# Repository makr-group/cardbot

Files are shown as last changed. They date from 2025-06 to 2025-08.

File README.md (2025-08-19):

    ╔══════════════════════════════════════════════════════════════════╗
    ║                                                                  ║
    ║     ██████╗ █████╗ ██████╗ ██████╗ ██████╗  ██████╗ ████████╗    ║
    ║    ██╔════╝██╔══██╗██╔══██╗██╔══██╗██╔══██╗██╔═══██╗╚══██╔══╝    ║
    ║    ██║     ███████║██████╔╝██║  ██║██████╔╝██║   ██║   ██║       ║
    ║    ██║     ██╔══██║██╔══██╗██║  ██║██╔══██╗██║   ██║   ██║       ║
    ║    ╚██████╗██║  ██║██║  ██║██████╔╝██████╔╝╚██████╔╝   ██║       ║
    ║     ╚═════╝╚═╝  ╚═╝╚═╝  ╚═╝╚═════╝ ╚═════╝  ╚═════╝    ╚═╝       ║
    ║                                                                  ║
    ╚══════════════════════════════════════════════════════════════════╝
    
      █▄▄ █▄█   █▀▄▀█ ▄▀█ █▄▀ █▀█
      █▄█ ░█░   █░▀░█ █▀█ █░█ █▀▄

**Cardbot** is a open source robotics project desinged to bring low costs entry level robots
to students and kids. This project was started by the non-profit Makr Group (aka Makr) to
bring robotics to under served communities in Omaha, Nebraska, USA. With the goal to
kickstart intrest in technology and robotics. The Project is ongoing and slowly growing with 
the capbilites of the robots.

Cardbot is shared under the **Creative Commons Attribution-ShareAlike 4.0 International** license.

## Current Features

- Controller driven Bots with a programmable autonomus mode
- Phone Driven Bots (Broken)
- 3D printer files
- Laser cutter files
- Build Instuctions

## Planned Features

- Full programming instuctions
- Class lesson plans
- Alternative Build Lists

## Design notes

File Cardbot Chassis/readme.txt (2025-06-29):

This folder contains all files related to the cardbot chassis.

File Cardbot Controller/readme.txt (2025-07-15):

Code and Files for Cardbot controllers.

Adruino IDE addons:

Board:
arduino-esp32 by expressif: https://github.com/espressif/arduino-esp32

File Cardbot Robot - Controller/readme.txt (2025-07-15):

Code for controller based Cardbots.

Adruino IDE addons:

Board:
arduino-esp32 by expressif: https://github.com/espressif/arduino-esp32

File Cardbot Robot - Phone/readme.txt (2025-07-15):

Code for phone/wifi controlled cardbots.

Adruino IDE addons:

Board:
arduino-esp32 by expressif: https://github.com/espressif/arduino-esp32

External Libaries:
AsyncTCP by ESP32Async: https://github.com/ESP32Async/AsyncTCP
ESPAsyncWebServer by ESP32Async: https://github.com/ESP32Async/ESPAsyncWebServer
ArduinoJson by Benoît Blanchon: https://github.com/bblanchon/ArduinoJson

Plugins:
arduino-littlefs-upload by Earle F. Philhower, III: https://github.com/earlephilhower/arduino-littlefs-upload

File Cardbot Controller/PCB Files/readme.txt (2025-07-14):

Files for Controller PCB both Gerber and KiCad.

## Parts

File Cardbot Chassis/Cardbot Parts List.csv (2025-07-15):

Item | Link | Per Kit
Jumpers | https://www.amazon.com/dp/B07XMH7MPL?ref_=ppx_hzsearch_conn_dt_b_fed_asin_title_3&th=1 | -
Red | - | 3
Black | - | 2
White | - | 2
Orange | - | 2
Yellow | - | 1
Purple | - | 1
Grey | - | 2
Brown | - | 2
Green | - | 1
Blue | - | 2
Active Components
Xaio Esp32C3 | https://www.digikey.com/en/products/detail/seeed-technology-co-ltd/113991054/16652880 | 1
5v Buck Converters | https://www.amazon.com/dp/B0BVFTSSSC?ref=ppx_yo2ov_dt_b_fed_asin_title&th=1 | 1
H Bridge | https://www.digikey.com/en/products/detail/adafruit-industries-llc/4489/11594498 | 2
TT Motor | https://www.amazon.com/dp/B09N6NXP4H?ref=ppx_yo2ov_dt_b_fed_asin_title | 2
9v Battery | https://www.amazon.com/dp/B07MWPHV25?ref=ppx_yo2ov_dt_b_fed_asin_title | 1
Passive Componets
Bread Board | https://www.amazon.com/dp/B07LFD4LT6?ref=ppx_yo2ov_dt_b_fed_asin_title | 1
Button (Short) | https://www.amazon.com/dp/B01CGMP9GY?ref=ppx_yo2ov_dt_b_fed_asin_title | 1
7 pin Headers | https://www.digikey.com/en/products/detail/adam-tech/PH1-07-UA/9830505 | 2
Switch | https://www.amazon.com/dp/B099MRCDG8?ref=ppx_yo2ov_dt_b_fed_asin_title&th=1 | 1
9v Battery Lead | https://www.amazon.com/dp/B083QFMXXW?ref=ppx_yo2ov_dt_b_fed_asin_title | 1
2-pos Terminal Block | https://www.amazon.com/dp/B01MT4LC0F?ref=ppx_yo2ov_dt_b_fed_asin_title | 1
Chassis Componets
Body | https://github.com/makr-group/cardbot/tree/main/cardbot%20chassis | 1
Connor Bracket | https://github.com/makr-group/cardbot/tree/main/cardbot%20chassis | 2
Connor Connector | https://github.com/makr-group/cardbot/tree/main/cardbot%20chassis | 4
Tail | https://github.com/makr-group/cardbot/tree/main/cardbot%20chassis | 1
Battery Holder | https://github.com/makr-group/cardbot/tree/main/cardbot%20chassis | 1
Pin | https://github.com/makr-group/cardbot/tree/main/cardbot%20chassis | 2

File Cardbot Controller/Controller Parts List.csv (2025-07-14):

Item | Link | Per Controller
Xaio Esp32C3 | https://www.digikey.com/en/products/detail/seeed-technology-co-ltd/113991054/16652880 | 1
Buttons (Tall) | https://www.digikey.com/en/products/detail/e-switch/TL1105BF160Q/1358 | 4
Controller PCB | https://github.com/makr-group/cardbot/tree/582c8274fbbf508515f54be0faa1b344a32cff6f/cardbot_%20controller_controlled/controller/PCB%20files | 1
Button Cap | https://github.com/makr-group/cardbot/tree/582c8274fbbf508515f54be0faa1b344a32cff6f/cardbot_%20controller_controlled/controller/3d-printed%20files | 1
Battery Holder | https://github.com/makr-group/cardbot/tree/582c8274fbbf508515f54be0faa1b344a32cff6f/cardbot_%20controller_controlled/controller/3d-printed%20files | 1
Bottom Plate | https://github.com/makr-group/cardbot/tree/582c8274fbbf508515f54be0faa1b344a32cff6f/cardbot_%20controller_controlled/controller/3d-printed%20files | 1
Face Plate | https://github.com/makr-group/cardbot/tree/582c8274fbbf508515f54be0faa1b344a32cff6f/cardbot_%20controller_controlled/controller/3d-printed%20files | 1

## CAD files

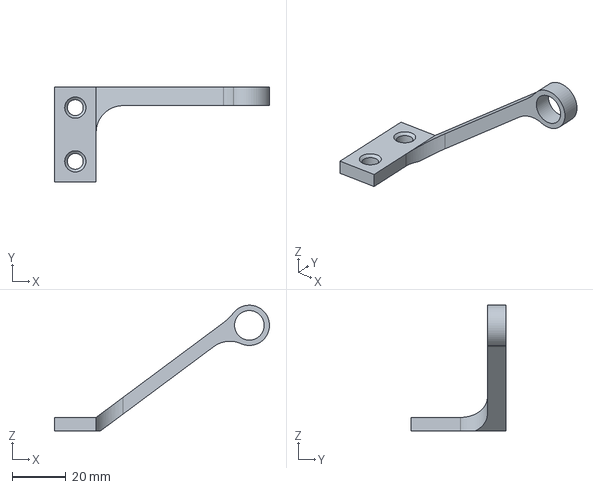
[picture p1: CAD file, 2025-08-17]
Cardbot Chassis/Cardbot Body - Tail.step
80.0 x 35.5 x 46.7 mm

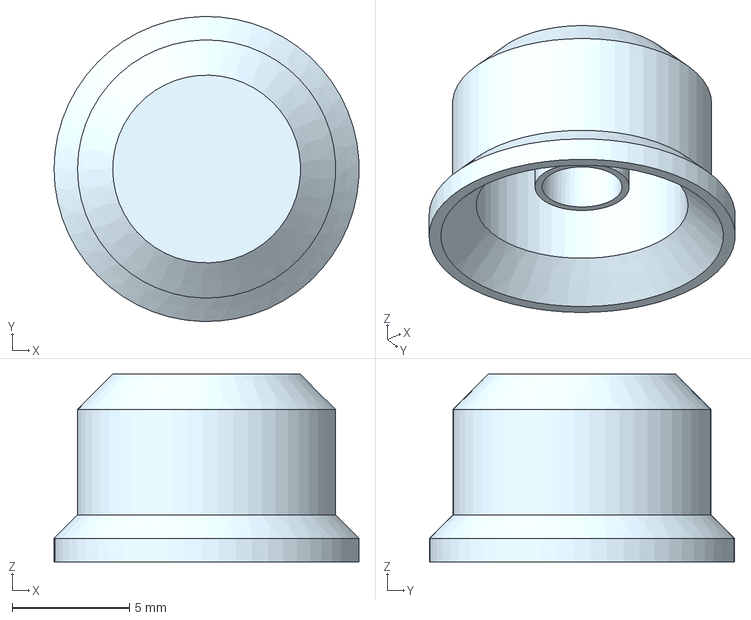
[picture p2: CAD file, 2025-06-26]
Cardbot Controller/3d-printed Files/Controller - Button Cap.step
13.0 x 13.0 x 8.00 mm

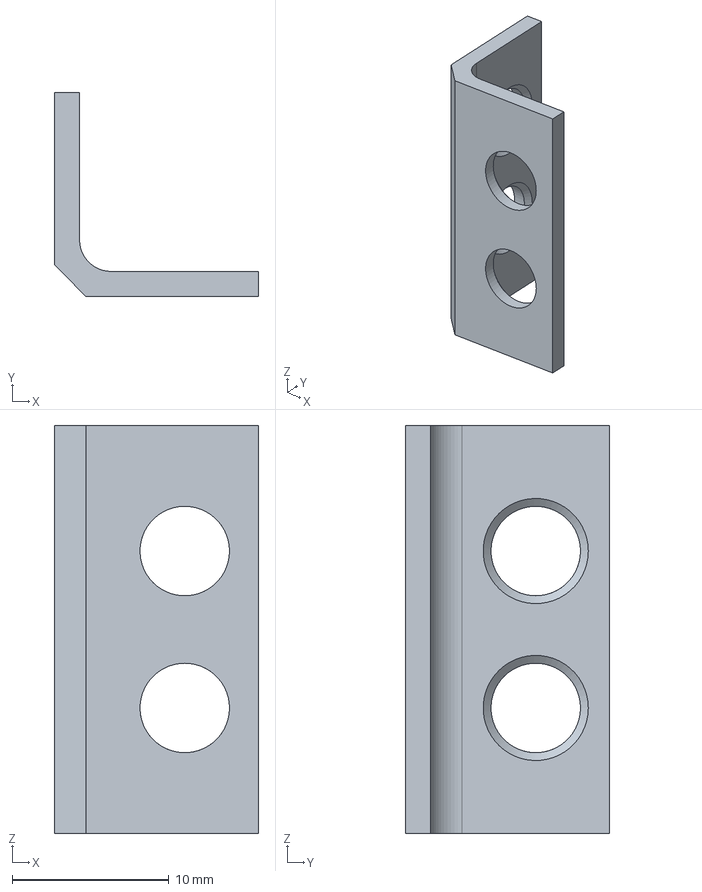
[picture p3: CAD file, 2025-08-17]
Cardbot Chassis/Cardbot Body - Corner Bracket.step
13.0 x 13.0 x 26.0 mm

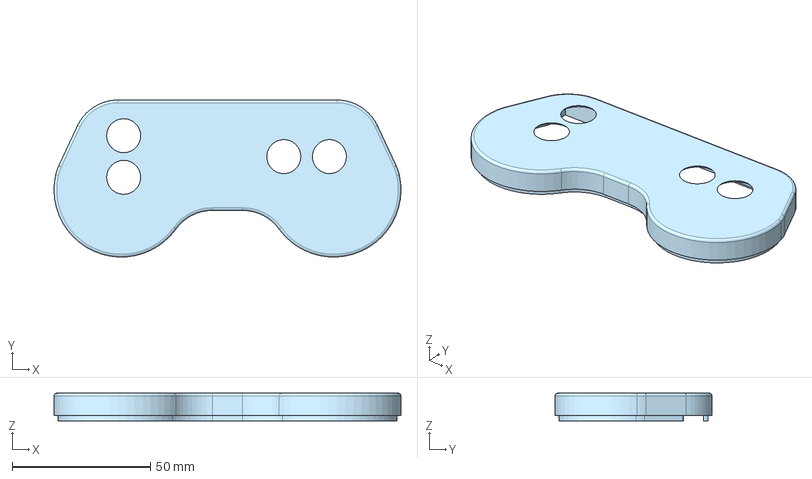
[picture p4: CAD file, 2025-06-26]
Cardbot Controller/3d-printed Files/Controller - Face Plate.step
125.7 x 56.9 x 10.0 mm

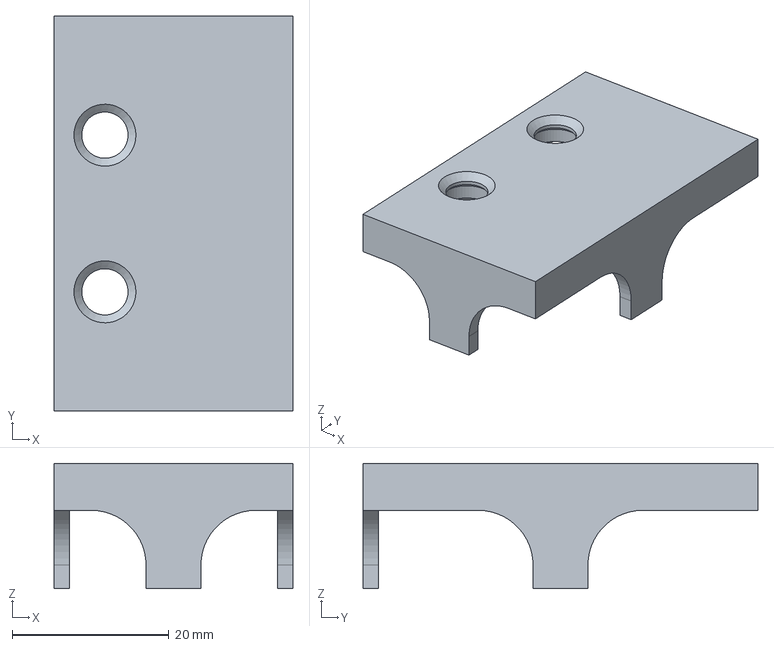
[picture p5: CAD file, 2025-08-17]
Cardbot Chassis/Cardbot Body - Battery Tray.step
30.5 x 50.4 x 16.0 mm

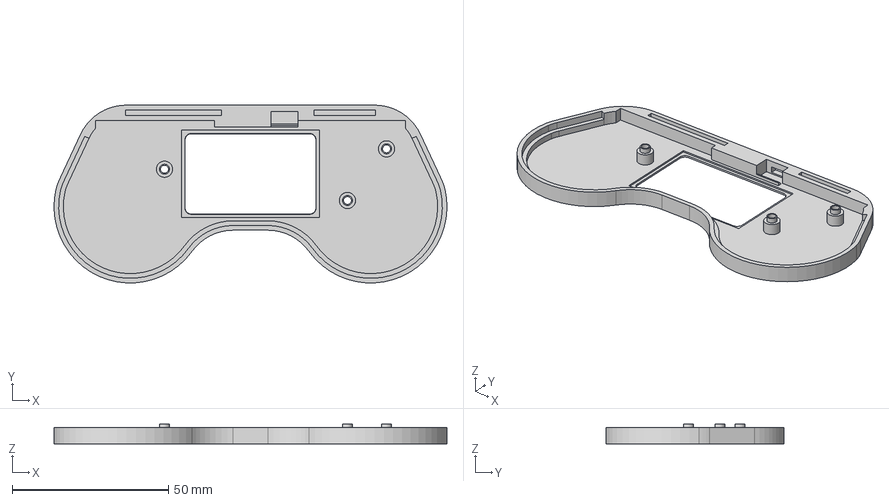
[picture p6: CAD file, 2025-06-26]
Cardbot Controller/3d-printed Files/Controller - Bottom Plate.step
125.7 x 56.9 x 6.25 mm

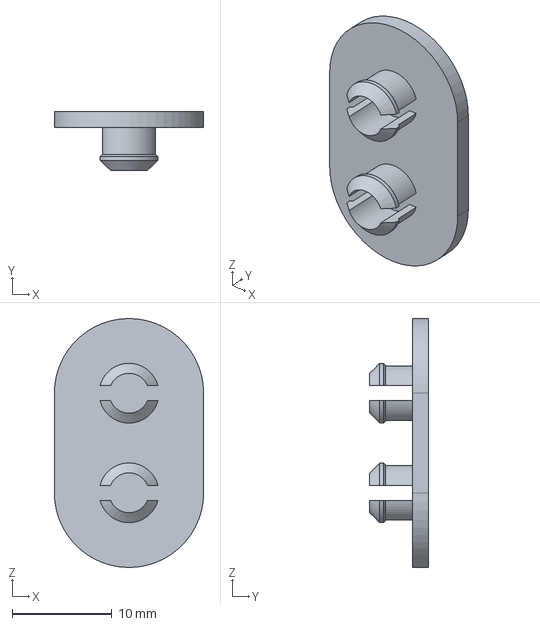
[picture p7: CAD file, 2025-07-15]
Cardbot Chassis/Cardbot Body - Corner Connector.step
15.0 x 5.90 x 25.0 mm

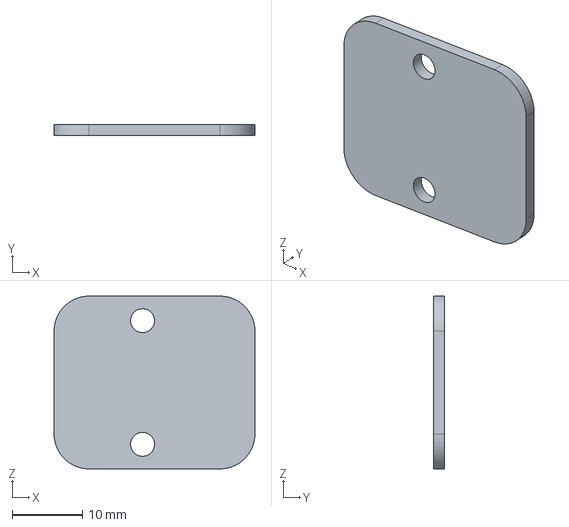
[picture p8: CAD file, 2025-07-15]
Cardbot Chassis/Cardbot Body - Motor Plate.step
28.6 x 1.60 x 24.6 mm

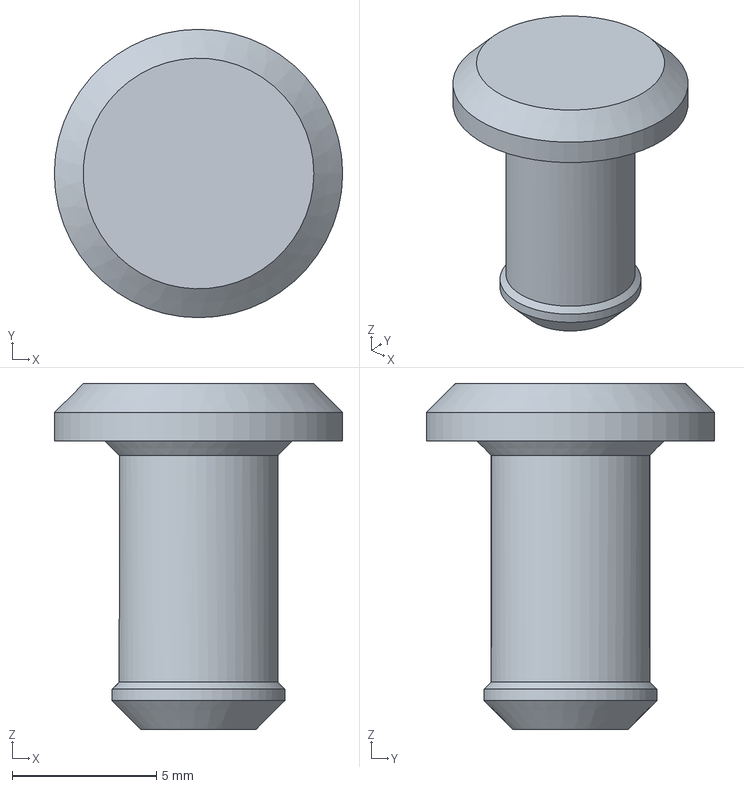
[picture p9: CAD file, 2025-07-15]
Cardbot Chassis/Cardbot Body - Tail Pin.step
10.0 x 10.0 x 12.0 mm

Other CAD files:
Cardbot Controller/3d-printed Files/Controller - Battery Holder.step
Cardbot Chassis/Cardbot Body - Battery Tray.stl
Cardbot Chassis/Cardbot Body - Corner Bracket.stl
Cardbot Chassis/Cardbot Body - Corner Connector.stl
Cardbot Chassis/Cardbot Body - Motor Plate.stl
Cardbot Chassis/Cardbot Body - Tail Pin.stl
Cardbot Chassis/Cardbot Body - Tail.stl
Cardbot Controller/3d-printed Files/Controller - Battery Holder.stl
Cardbot Controller/3d-printed Files/Controller - Bottom Plate.stl
Cardbot Controller/3d-printed Files/Controller - Button Cap.stl
Cardbot Controller/3d-printed Files/Controller - Face Plate.stl

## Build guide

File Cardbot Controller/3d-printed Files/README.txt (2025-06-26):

STL and Step files for cardbot controllers

STLs are designed to be printed with PLA and are untested 
with PETG, ABS, and ABS.

Tested with:

Printer: Ultimaker 3 Extended
Settings:
  Material: Generic PLA
  Walls: 4
  Supports: No *
  Bed Adhesion: 5mm Skirt
Notes:
* No supports is important to keep the USB-C port clean
  of unwanted material for "Controller - Face Plate". Supports 
  might be needed if your  printer cannot handle the that length 
  of bridging.

Printer Bambu labs P1S
Settings:
  Material: Bambu Labs Basic PLA
  Walls: 4
  Wall Generator: Arachne *
  Supports: No **
Notes:
  * Arachne is required for the buttons walls classic generation
    will not print inner button caps
  
**  No supports is important to keep the USB-C port clean
    of unwanted material for "Controller - Face Plate". Supports 
    might be needed if your  printer cannot handle the that length 
    of bridging.

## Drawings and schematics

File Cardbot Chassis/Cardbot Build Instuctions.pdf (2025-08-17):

1.

+

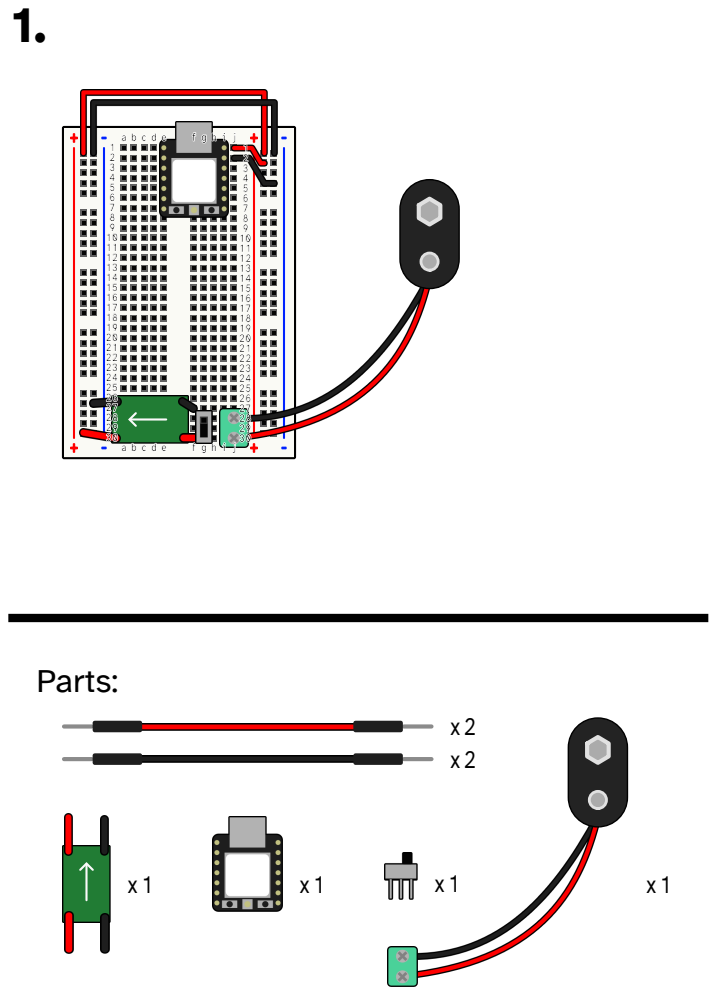
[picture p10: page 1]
Parts:

2.

+

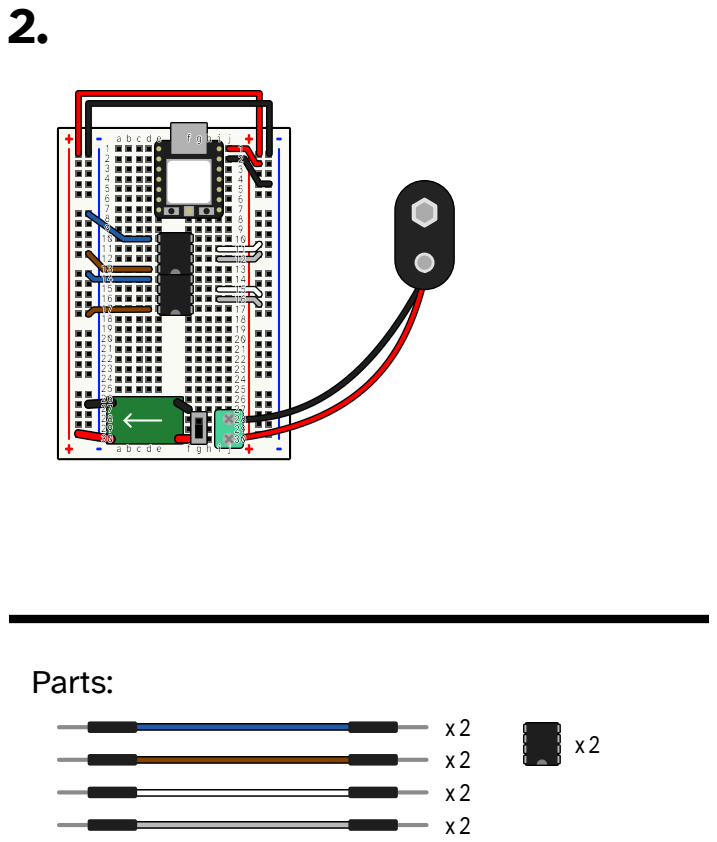
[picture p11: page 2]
Parts:

3.

# Parts: ⁺ - + -

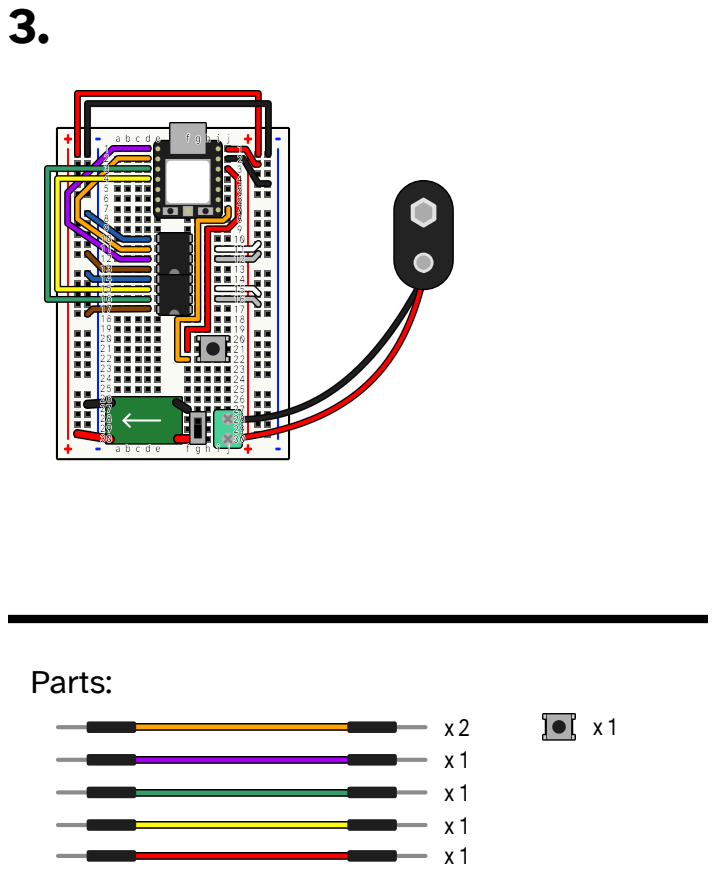
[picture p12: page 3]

4.

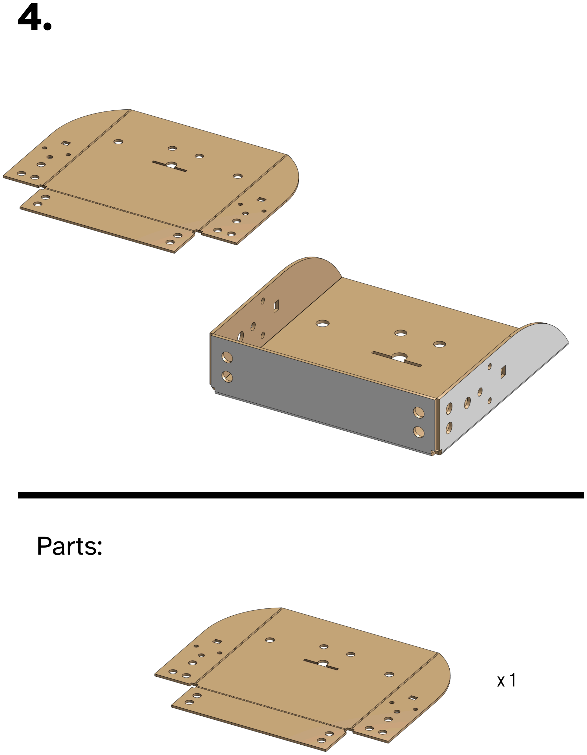
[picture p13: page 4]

# Parts:

x1

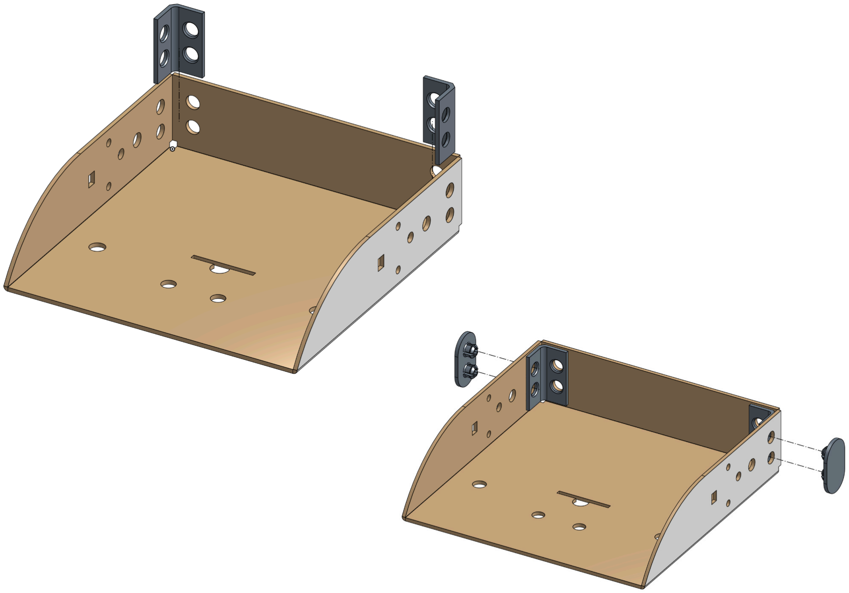
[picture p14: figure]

# Parts:

5.

x2 | x2

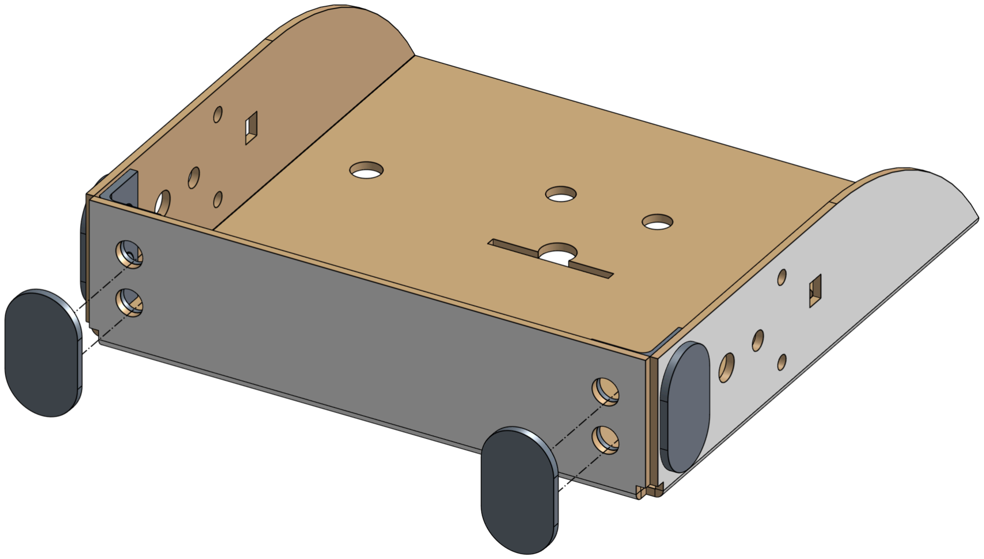
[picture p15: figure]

# Parts:

6.

x2

7.

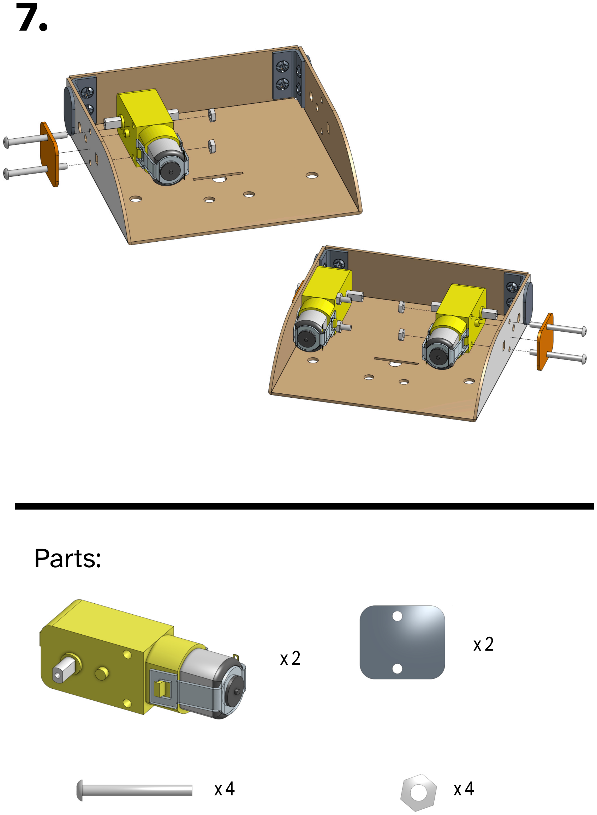
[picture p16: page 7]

# Parts:

x2 | x2
x4 | x4

8.

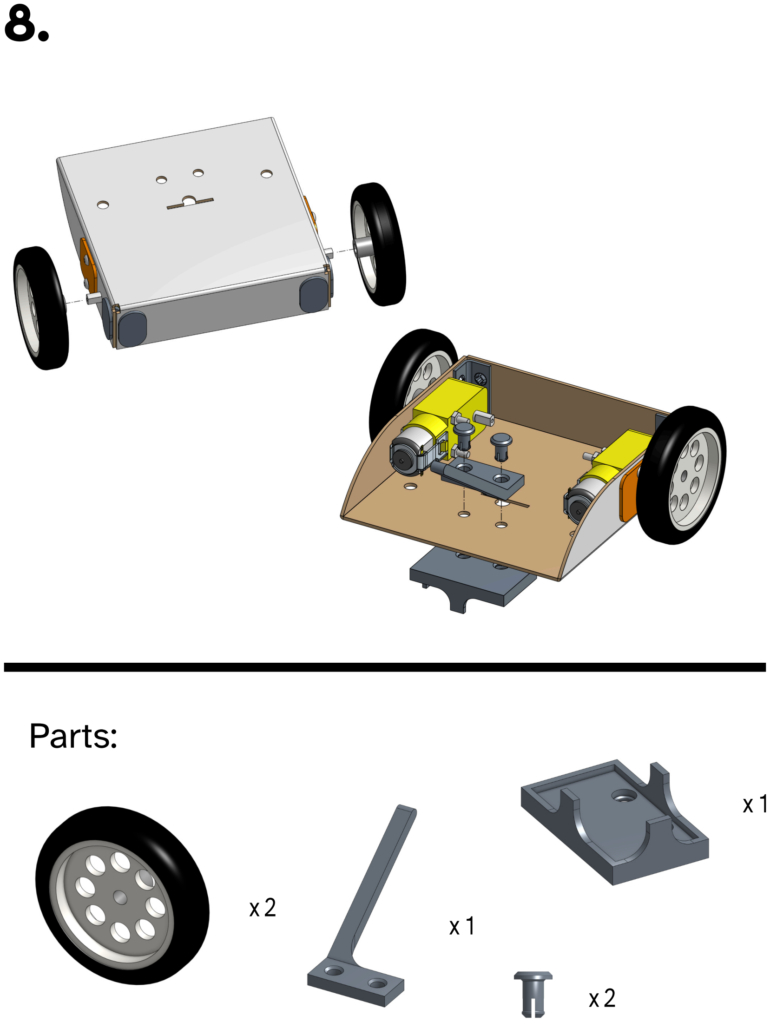
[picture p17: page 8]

# Parts:

x2

x2

x1

x1

9.

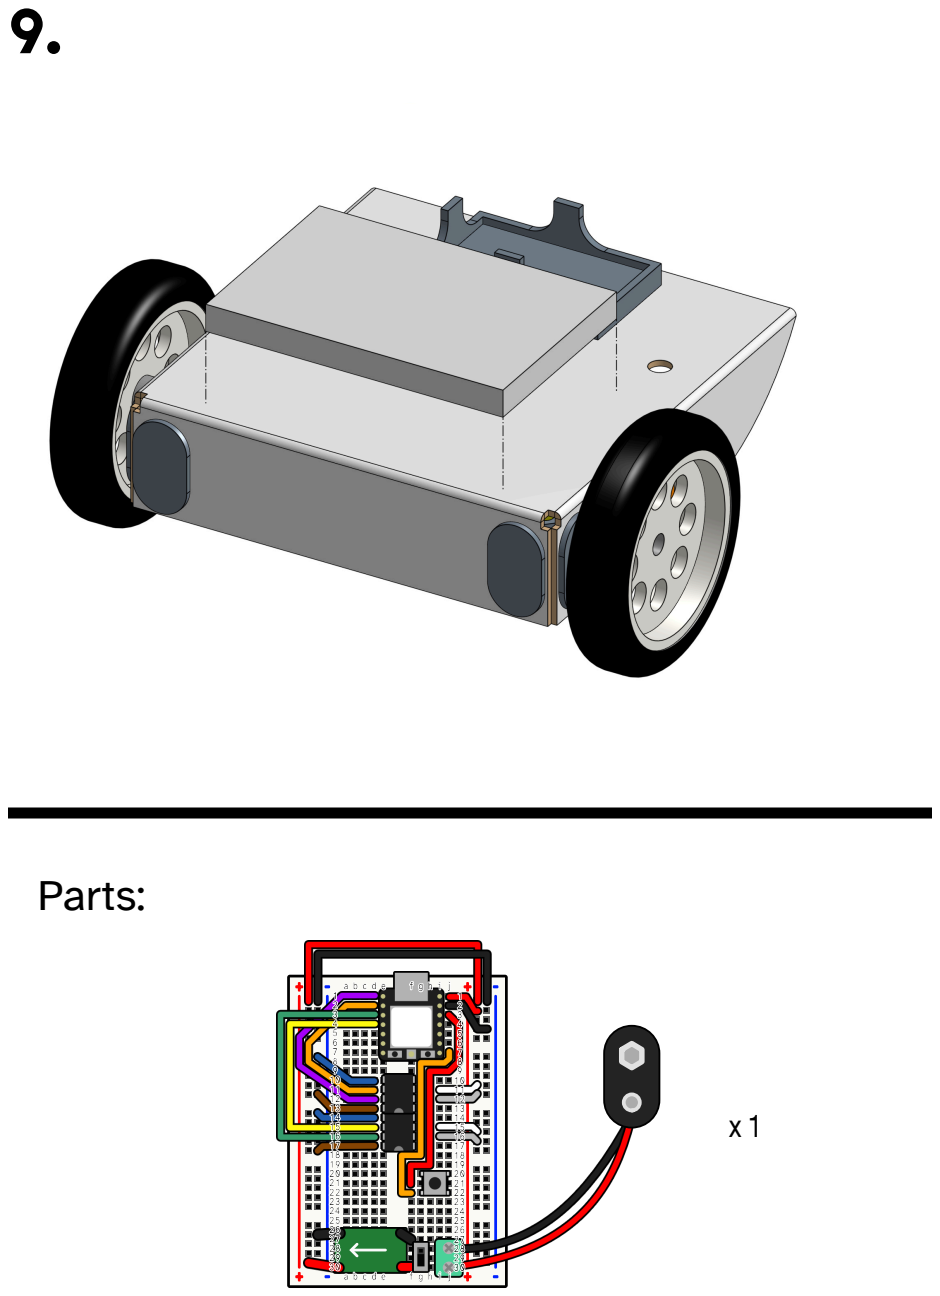
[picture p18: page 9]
Parts:

10.

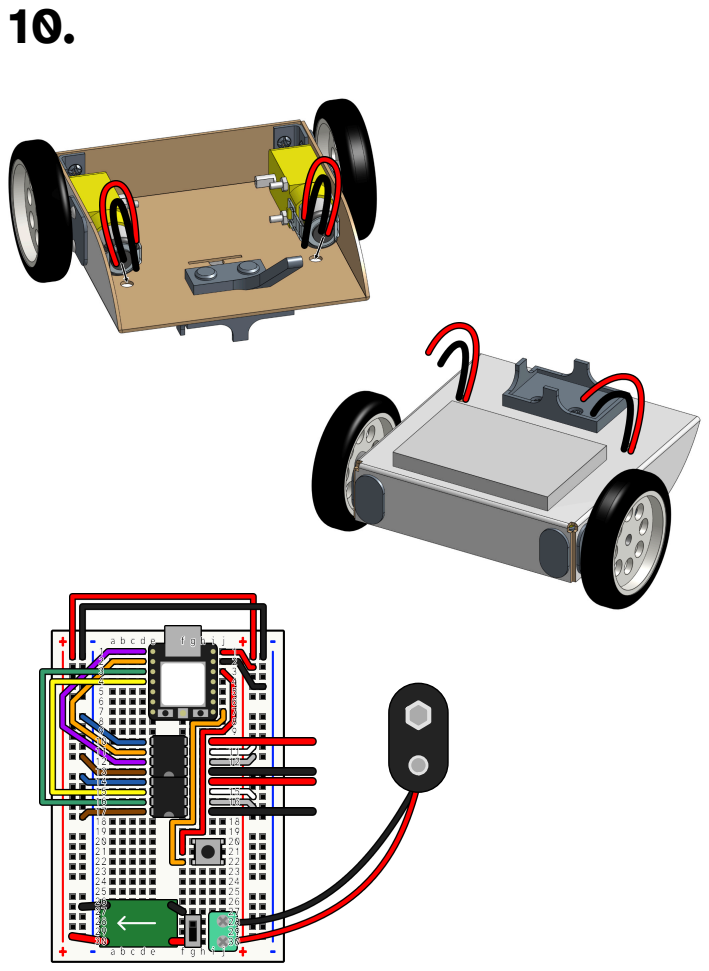
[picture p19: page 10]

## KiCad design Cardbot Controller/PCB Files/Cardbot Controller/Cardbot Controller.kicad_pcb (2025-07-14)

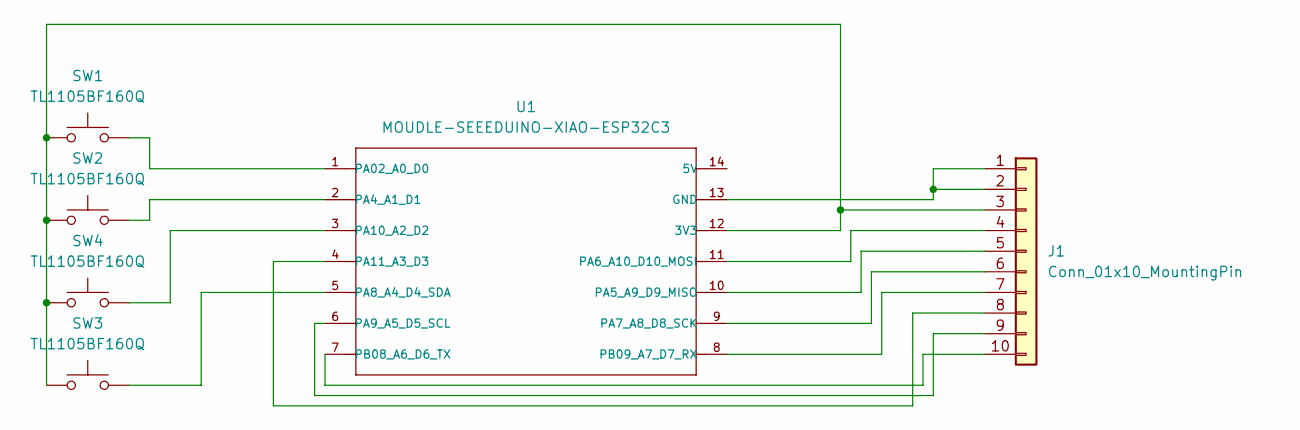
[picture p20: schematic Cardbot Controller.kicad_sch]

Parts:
J1: Conn_01x10_MountingPin
SW1, SW2, SW3, SW4: TL1105BF160Q
U1: MOUDLE-SEEEDUINO-XIAO-ESP32C3; MOUDLE14P-SMD-2.54-21X17.8MM

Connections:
unnamed: J1.1, J1.2, U1.13 (GND)
unnamed: J1.3, SW1.1, SW2.1, SW3.1, SW4.1, U1.12 (3V3)
unnamed: J1.4, U1.11 (PA6_A10_D10_MOSI)
unnamed: J1.5, U1.10 (PA5_A9_D9_MISO)
unnamed: J1.6, U1.9 (PA7_A8_D8_SCK)
unnamed: J1.7, U1.8 (PB09_A7_D7_RX)
unnamed: J1.8, U1.4 (PA11_A3_D3)
unnamed: J1.9, U1.6 (PA9_A5_D5_SCL)
unnamed: J1.10, U1.7 (PB08_A6_D6_TX)
unnamed: SW1.2, U1.1 (PA02_A0_D0)
unnamed: SW2.2, U1.2 (PA4_A1_D1)
unnamed: SW3.2, U1.5 (PA8_A4_D4_SDA)
unnamed: SW4.2, U1.3 (PA10_A2_D2)

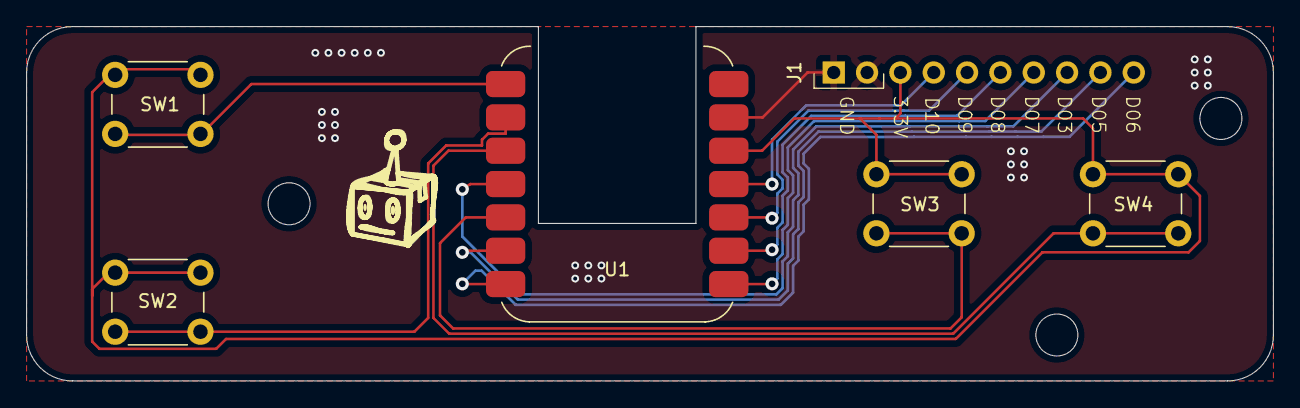
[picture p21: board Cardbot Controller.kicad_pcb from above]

Board: 2 copper layers, 95.0 x 27.0 mm, 6 parts (0 on the bottom side), 13 nets.

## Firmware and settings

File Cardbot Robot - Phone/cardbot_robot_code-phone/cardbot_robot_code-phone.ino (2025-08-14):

// ╔══════════════════════════════════════════════════════════════════╗
// ║                                                                  ║
// ║     ██████╗ █████╗ ██████╗ ██████╗ ██████╗  ██████╗ ████████╗    ║
// ║    ██╔════╝██╔══██╗██╔══██╗██╔══██╗██╔══██╗██╔═══██╗╚══██╔══╝    ║
// ║    ██║     ███████║██████╔╝██║  ██║██████╔╝██║   ██║   ██║       ║
// ║    ██║     ██╔══██║██╔══██╗██║  ██║██╔══██╗██║   ██║   ██║       ║
// ║    ╚██████╗██║  ██║██║  ██║██████╔╝██████╔╝╚██████╔╝   ██║       ║
// ║     ╚═════╝╚═╝  ╚═╝╚═╝  ╚═╝╚═════╝ ╚═════╝  ╚═════╝    ╚═╝       ║
// ║                                                                  ║
// ╚══════════════════════════════════════════════════════════════════╝
//
//  █▄▄ █▄█   █▀▄▀█ ▄▀█ █▄▀ █▀█
//  █▄█ ░█░   █░▀░█ █▀█ █░█ █▀▄
//
//  Cardbot Robot Code - Phone
//  Version: 0.1.1
//  Date: 7/14/2025
//  Cardbot code for phone control only
//    - button input is disabled
//  Carbot Version: 1.0 - 1.2

#include <LittleFS.h>
#include <WiFi.h>
#include <ArduinoJson.h>
#include <ESPAsyncWebServer.h>


#define LM_PIN_FORWARD 5
#define LM_PIN_BACKWARD 4
#define RM_PIN_FORWARD 3
#define RM_PIN_BACKWARD 2
#define HTTP_PORT 80

//-------------------------------------

const char CARDBOT_NAME[] = "NAME HERE";

//-------------------------------------

const char *CARDBOT_SSID = CARDBOT_NAME;
const char *CARDBOT_PASSWORD = "PASSWORD_HERE";
IPAddress subnet(255,255,255,0);

// input array
bool input_array[4];
// forward button, backward button, left Button, right Button

//  █▀▄▀█ █▀█ ▀█▀ █▀█ █▀█   █▀ █▀▀ ▀█▀ █░█ █▀█
//  █░▀░█ █▄█ ░█░ █▄█ █▀▄   ▄█ ██▄ ░█░ █▄█ █▀▀

struct motor
{
  uint8_t forward_pin;
  uint8_t backward_pin;
  bool moving;

  void forward()
  {
    digitalWrite(forward_pin, HIGH);
    digitalWrite(backward_pin, LOW);
    moving = true;
  }

  void backward()
  {
    digitalWrite(forward_pin, LOW);
    digitalWrite(backward_pin, HIGH);
    moving = true;
  }

  void stop()
  {
    digitalWrite(forward_pin, LOW);
    digitalWrite(backward_pin, LOW);
    moving = false;
  }
};

motor left_motor = {LM_PIN_FORWARD, LM_PIN_BACKWARD};
motor right_motor = {RM_PIN_FORWARD, RM_PIN_BACKWARD};

//  █▀█ █▀█ █▄▄ █▀█ ▀█▀   █▀ █▀▀ ▀█▀ █░█ █▀█
//  █▀▄ █▄█ █▄█ █▄█ ░█░   ▄█ ██▄ ░█░ █▄█ █▀▀

void forwards()
{
  left_motor.forward();
  right_motor.forward();
}
void backwards()
{
  left_motor.backward();
  right_motor.backward();
}
void pivotLeft()
{
  left_motor.backward();
  right_motor.forward();
}
void pivotRight()
{
  left_motor.forward();
  right_motor.backward();
}
void turnLeftForward()
{
  left_motor.stop();
  right_motor.forward();
}
void turnLeftBackward()
{
  left_motor.stop();
  right_motor.backward();
}
void turnRigthForward()
{
  left_motor.forward();
  right_motor.stop();
}
void turnRightBackward()
{
  left_motor.backward();
  right_motor.stop();
}
void stop()
{
  left_motor.stop();
  right_motor.stop();
}

//  █▀▀ █ █░░ █▀▀   █▀ █▄█ ▀█▀ █▀▀ █▀▄▀█   █▀ █▀▀ ▀█▀ █░█ █▀█
//  █▀░ █ █▄▄ ██▄   ▄█ ░█░ ░█░ ██▄ █░▀░█   ▄█ ██▄ ░█░ █▄█ █▀▀

void initLittleFS()
{
  if (!LittleFS.begin())
  {
    Serial.println("Cannot mount LittleFS volume...");
  }
}

//  █░█░█ █▀▀ █▄▄ █▀ █▀▀ █▀█ █░█ █▀▀ █▀█   █▀ █▀▀ ▀█▀ █░█ █▀█
//  ▀▄▀▄▀ ██▄ █▄█ ▄█ ██▄ █▀▄ ▀▄▀ ██▄ █▀▄   ▄█ ██▄ ░█░ █▄█ █▀▀

AsyncWebServer server(HTTP_PORT);
AsyncWebSocket ws("/ws");

boolean moving()
{
  if (left_motor.moving || right_motor.moving)
  {
    return true;
  }
  else
  {
    return false;
  }
}

void onRootRequest(AsyncWebServerRequest *request)
{
  request->send(LittleFS, "/index.html", "text/html", false);
}

void initWebServer()
{
  server.on("/", onRootRequest);
  server.serveStatic("/", LittleFS, "/").setDefaultFile("index.html");
  server.begin();
}

void initWiFi()
{
  WiFi.mode(WIFI_AP);
  WiFi.softAPConfig(IPAddress(192,168,10,10), IPAddress(192,168,10,1), subnet);
  WiFi.softAP(CARDBOT_SSID, CARDBOT_PASSWORD);
  Serial.println(WiFi.softAPIP().toString().c_str());
}

void notifyClients(const char *type, const char *data)
{
  JsonDocument doc;
  doc["type"] = type;
  doc["data"] = data;
  char output[64];
  size_t len = serializeJson(doc, output);
  ws.textAll(output, len);
}

// converts local ip form type IPADDRESS to char
const char *ipChar()
{
  uint8_t ipArray[] = {WiFi.localIP()[0], '.', WiFi.localIP()[1], '.', WiFi.localIP()[2], '.', WiFi.localIP()[3]};
  const char *charIP = reinterpret_cast<const char *>(ipArray);
  return charIP;
}


//  █░█░█ █▀▀ █▄▄   █░█ ▄▀█ █▄░█ █▀▄ █░░ █▀▀ █▀█
//  ▀▄▀▄▀ ██▄ █▄█   █▀█ █▀█ █░▀█ █▄▀ █▄▄ ██▄ █▀▄

// handles action messages
// json format {"type": "action", "data":"(button action)"}
void actionHandler(const char *data)
{
  if (strcmp(data, "up") == 0)
  {
    input_array[0] = 1;
    Serial.println("Up");
  }
  else if (strcmp(data, "dp") == 0)
  {
    input_array[1] = 1;
    Serial.println("DP");
  }
  else if (strcmp(data, "lp") == 0)
  {
    input_array[2] = 1;
    Serial.println("LP");
  }
  else if (strcmp(data, "rp") == 0)
  {
    input_array[3] = 1;
    Serial.println("RP");
  }
  else if (strcmp(data, "ur") == 0)
  {
    input_array[0] = 0;
    Serial.println("UR");
  }
  else if (strcmp((char *)data, "dr") == 0)
  {
    input_array[1] = 0;
    Serial.println("DR");
  }
  else if (strcmp((char *)data, "lr") == 0)
  {
    input_array[2] = 0;
    Serial.println("LR");
  }
  else if (strcmp((char *)data, "rr") == 0)
  {
    input_array[3] = 0;
    Serial.println("RR");
  }
  else
  {
    input_array[3] = 0;
    input_array[2] = 0;
    input_array[1] = 0;
    input_array[0] = 0;
  }
}
// handles request messages
// json format {"type": "request", "data":"(request type)"}
void requestHandler(const char *data)
{
  if (strcmp(data, "ip"))
  {
    notifyClients("ip", ipChar());
    return;
  }
  else if (strcmp(data, "name"))
  {
    notifyClients("name", CARDBOT_NAME);
    return;
  }
  else
  {
    return;
  }
}
// controls the robot inturpets input array
void robotControl()
{
  static bool updateCheck[4];

  if (updateCheck[0] != input_array[0] or updateCheck[1] != input_array[1] or updateCheck[2] != input_array[2] or
      updateCheck[3] != input_array[3])
  {

    // Forwards
    if (input_array[0] == true && input_array[1] == false && input_array[2] == false && input_array[3] == false)
    {
      forwards();
      notifyClients("motor", "on");
      Serial.print("Forward");
    }
    // Backwards
    else if (input_array[0] == false && input_array[1] == true && input_array[2] == false && input_array[3] == false)
    {
      backwards();
      notifyClients("motor", "on");
      Serial.print("Backwards");
    }
    // Pivot left
    else if (input_array[0] == false && input_array[1] == false && input_array[2] == true && input_array[3] == false)
    {
      pivotLeft();
      notifyClients("motor", "on");
      Serial.print("Pivot Left");
    }
    // Pivot right
    else if (input_array[0] == false && input_array[1] == false && input_array[2] == false && input_array[3] == true)
    {
      pivotRight();
      notifyClients("motor", "on");
      Serial.print("Pivot Right");
    }
    // Turn left forward
    else if (input_array[0] == true && input_array[1] == false && input_array[2] == true && input_array[3] == false)
    {
      turnLeftForward();
      notifyClients("motor", "on");
      Serial.print("Turn Left Forward");
    }
    // Turn left backward
    else if (input_array[0] == false && input_array[1] == true && input_array[2] == true && input_array[3] == false)
    {
      turnLeftBackward();
      notifyClients("motor", "on");
      Serial.print("Turn Left Backwards");
    }
    // Turn right forwards
    else if (input_array[0] == true && input_array[1] == false && input_array[2] == false && input_array[3] == true)
    {
      turnRigthForward();
      notifyClients("motor", "on");
      Serial.print("Turn Right Forwards");
    }
    // Turn right backward
    else if (input_array[0] == false && input_array[1] == true && input_array[2] == false && input_array[3] == true)
    {
      turnRightBackward();
      notifyClients("motor", "on");
      Serial.print("Turn Right Backwards");
    }
    else
    {
      stop();
      notifyClients("motor", "off");
    }
    updateCheck[0] = input_array[0];
    updateCheck[1] = input_array[1];
    updateCheck[2] = input_array[2];
    updateCheck[3] = input_array[3];
  }
}
// message type handler
void messageTypeHandler(const char *type, JsonDocument doc)
{
  if (strcmp(type, "action") == 0)
  {
    actionHandler(doc["data"]);
    Serial.println("Action Triggered");
    return;
  }
  else if (strcmp(type, "request") == 0)
  {
    requestHandler(doc["data"]);
    Serial.println("Request Triggered");
    return;
  }
  else
  {
    return;
  }
}
// message handler
void handleWebSocketMessage(void *arg, uint8_t *data, size_t len)
{
  JsonDocument doc;
  AwsFrameInfo *info = (AwsFrameInfo *)arg;
  int typeInt;
  DeserializationError err = deserializeJson(doc, data);
  if (err)
  {
    Serial.print(F("deserializeJson() failed with code "));
    Serial.println(err.c_str());
    return;
  }
  if (info->final && info->index == 0 && info->len == len && info->opcode == WS_TEXT)
  {

    deserializeJson(doc, data);
    const char *type = doc["type"];
    Serial.println(type);
    messageTypeHandler(type, doc);
  }
}

// event handler
void onEvent(AsyncWebSocket *server,      
             AsyncWebSocketClient *client, 
             AwsEventType type,            
             void *arg,                    
             uint8_t *data,               
             size_t len)
{
  switch (type)
  {
  case WS_EVT_CONNECT:
    Serial.printf("WebSocket client #%u connected from %s\n", client->id(), client->remoteIP().toString().c_str());
    notifyClients("name", CARDBOT_NAME);
    notifyClients("motor", "off");
    stop();
    break;
  case WS_EVT_DISCONNECT:
    Serial.printf("WebSocket client #%u disconnected\n", client->id());
    stop();
    break;
  case WS_EVT_DATA:
    handleWebSocketMessage(arg, data, len);
  case WS_EVT_PONG:
  case WS_EVT_ERROR:
    stop();
    break;
  }
}

void initWebSocket()
{
  ws.onEvent(onEvent);
  server.addHandler(&ws);
}

void setup()
{
  pinMode(left_motor.forward_pin, OUTPUT);
  pinMode(left_motor.backward_pin, OUTPUT);
  pinMode(right_motor.forward_pin, OUTPUT);
  pinMode(right_motor.backward_pin, OUTPUT);

  Serial.begin(115200);
  delay(500);

  initLittleFS();
  initWiFi();
  initWebServer();
  initWebSocket();
}

void loop()
{
  ws.cleanupClients();
  robotControl();
}

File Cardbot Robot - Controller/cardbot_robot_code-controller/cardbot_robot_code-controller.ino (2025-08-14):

// ╔══════════════════════════════════════════════════════════════════╗
// ║                                                                  ║
// ║     ██████╗ █████╗ ██████╗ ██████╗ ██████╗  ██████╗ ████████╗    ║
// ║    ██╔════╝██╔══██╗██╔══██╗██╔══██╗██╔══██╗██╔═══██╗╚══██╔══╝    ║
// ║    ██║     ███████║██████╔╝██║  ██║██████╔╝██║   ██║   ██║       ║
// ║    ██║     ██╔══██║██╔══██╗██║  ██║██╔══██╗██║   ██║   ██║       ║
// ║    ╚██████╗██║  ██║██║  ██║██████╔╝██████╔╝╚██████╔╝   ██║       ║
// ║     ╚═════╝╚═╝  ╚═╝╚═╝  ╚═╝╚═════╝ ╚═════╝  ╚═════╝    ╚═╝       ║
// ║                                                                  ║
// ╚══════════════════════════════════════════════════════════════════╝
//
//  █▄▄ █▄█   █▀▄▀█ ▄▀█ █▄▀ █▀█
//  █▄█ ░█░   █░▀░█ █▀█ █░█ █▀▄
//
//  Cardbot Robot Code - Controller
//  Version: 0.1.1
//  Date: 7/8/2025
//  Cardbot code for autonomous mode and controllers
//  Carbot Version: 1.2
//  Controller Version: 1.0

#define LM_PIN_FORWARD 5
#define LM_PIN_BACKWARD 4
#define RM_PIN_FORWARD 3
#define RM_PIN_BACKWARD 2

#define BUTTON_PIN 20

#include <WiFi.h>
#include <esp_now.h>

// Global Varibales
bool automonus_active = false;
uint16_t last_connection_check = 0;

//  █▀▄▀█ █▀█ ▀█▀ █▀█ █▀█   █▀ █▀▀ ▀█▀ █░█ █▀█
//  █░▀░█ █▄█ ░█░ █▄█ █▀▄   ▄█ ██▄ ░█░ █▄█ █▀▀

typedef struct motor {
  // Controls the motor's basic movements
  uint8_t f_pin;
  uint8_t b_pin;
  bool moving;

  void forward() {
    digitalWrite(f_pin, HIGH);
    digitalWrite(b_pin, LOW);
    moving = true;
  }

  void backward() {
    digitalWrite(f_pin, LOW);
    digitalWrite(b_pin, HIGH);
    moving = true;
  }

  void stop() {
    digitalWrite(f_pin, LOW);
    digitalWrite(b_pin, LOW);
    moving = false;
  }

  void setup(uint8_t forward_pin, uint8_t backward_pin) {
    f_pin = forward_pin;
    b_pin = backward_pin;
    pinMode(forward_pin, OUTPUT);
    pinMode(backward_pin, OUTPUT);
  }
};

motor left_motor;
motor right_motor;

//  █▀█ █▀█ █▄▄ █▀█ ▀█▀   █▀ █▀▀ ▀█▀ █░█ █▀█
//  █▀▄ █▄█ █▄█ █▄█ ░█░   ▄█ ██▄ ░█░ █▄█ █▀▀

void stop(int time = 0) {
  left_motor.stop();
  right_motor.stop();
  delay(time);
}
void forwards(int time = 0) {
  left_motor.forward();
  right_motor.forward();
  delay(time);
  if (time > 0) {
    delay(100);
  }
}
void backwards(int time = 0) {
  left_motor.backward();
  right_motor.backward();
  delay(time);
  if (time > 0) {
    delay(100);
  }
}
void pivotLeft(int time = 0) {
  left_motor.backward();
  right_motor.forward();
  delay(time);
  if (time > 0) {
    delay(100);
  }
}
void pivotRight(int time = 0) {
  left_motor.forward();
  right_motor.backward();
  delay(time);
  if (time > 0) {
    delay(100);
  }
}
void turnLeftForward(int time = 0) {
  left_motor.stop();
  right_motor.forward();
  delay(time);
  if (time > 0) {
    delay(100);
  }
}
void turnLeftBackward(int time = 0) {
  left_motor.stop();
  right_motor.backward();
  delay(time);
  if (time > 0) {
    delay(100);
  }
}
void turnRightForward(int time = 0) {
  left_motor.forward();
  right_motor.stop();
  delay(time);
  if (time > 0) {
    delay(50);
  }
}
void turnRightBackward(int time = 0) {
  left_motor.backward();
  right_motor.stop();
  delay(time);
  if (time > 0) {
    delay(50);
  }
}

//  █▀▀ █▀█ █▄░█ ▀█▀ █▀█ █▀█ █░░ █░░ █▀▀ █▀█   █▀ █▀▀ ▀█▀ █░█ █▀█
//  █▄▄ █▄█ █░▀█ ░█░ █▀▄ █▄█ █▄▄ █▄▄ ██▄ █▀▄   ▄█ ██▄ ░█░ █▄█ █▀▀

typedef struct controller_message {
  // message structure between
  int16_t joy_1_x_axis;
  int16_t joy_1_y_axis;
  bool up_state;
  bool down_state;
  bool left_state;
  bool right_state;
  uint16_t connection_check = 0;
};

controller_message controller;

// callback function on controller message
void controllerMode(const esp_now_recv_info_t *info, const uint8_t *incoming_data, int len) {

  memcpy(&controller, incoming_data, sizeof(controller));
  if (!automonus_active) {  
    // controller will be locked out in while in automonus mode 
    if (controller.up_state && controller.left_state) {
      turnLeftForward();
    } else if (controller.up_state && controller.right_state) {
      turnRightForward();
    } else if (controller.down_state && controller.left_state) {
      turnLeftBackward();
    } else if (controller.down_state && controller.right_state) {
      turnRightBackward();
    } else if (controller.left_state) {
      pivotLeft();
    } else if (controller.right_state) {
      pivotRight();
    } else if (controller.up_state) {
      forwards();
    } else if (controller.down_state) {
      backwards();
    } else {
      stop();
    }
  }
}

//  ▄▀█ █░█ ▀█▀ █▀█ █▀▄▀█ █▀█ █▄░█ █░█ █▀   █▀▄▀█ █▀█ █▀▄ █▀▀
//  █▀█ █▄█ ░█░ █▄█ █░▀░█ █▄█ █░▀█ █▄█ ▄█   █░▀░█ █▄█ █▄▀ ██▄

// automonus code to run on button press
void automonusMode() {
  // atonmonus code here
}

//  █▀ █▀▀ ▀█▀ █░█ █▀█
//  ▄█ ██▄ ░█░ █▄█ █▀▀

void setup() {
  left_motor.setup(LM_PIN_FORWARD, LM_PIN_BACKWARD);
  right_motor.setup(RM_PIN_FORWARD, RM_PIN_BACKWARD);

  pinMode(BUTTON_PIN, INPUT_PULLDOWN);

  WiFi.mode(WIFI_STA);

  // Initilize ESP-NOW
  if (esp_now_init() != ESP_OK) {
    return;
  }

  // Register callback function
  esp_now_register_recv_cb(controllerMode);
}

//  █▀▄▀█ ▄▀█ █ █▄░█   █░░ █▀█ █▀█ █▀█
//  █░▀░█ █▀█ █ █░▀█   █▄▄ █▄█ █▄█ █▀▀

// main control loop checks for button press and controller disconnect
void loop() {
  static unsigned long currentMillis;
  static unsigned long previousMillis = 0;

  //activates automonus_mode on button press
  if (digitalRead(BUTTON_PIN)) {
    automonus_active = true;  // locks out controller
    delay(1000);              // 1 sec delay befor start
    automonusMode();
    automonus_active = false;
  }

  currentMillis = millis();
  // checks for controller connections
  if (currentMillis - previousMillis >= 200) {
    previousMillis = currentMillis;

    if (controller.connection_check == last_connection_check) {
      controller.down_state = false;
      controller.up_state = false;
      controller.left_state = false;
      controller.right_state = false;
      stop();
    }

    last_connection_check = controller.connection_check;
  }
}

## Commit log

2025-06-24 Added Arduino code
2025-06-24 Create cardbot_controller_code.cpp
    Added raw c++ code for cardbot controller in Arduino format
2025-06-24 Added Arduino code for Cardbot Controller
2025-06-26 Created STEP files for controllers
    [Controller - Button Cap.step, Controller - Battery Holder.step, Controller - Bottom Plate.step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]
2025-06-26 Created controller STL files
    [Controller - Battery Holder.stl, Controller - Bottom Plate.stl, Controller - Button Cap.stl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]
2025-06-29 Added 3D Printed Parts
    [Cardbot - Corner Bracket.stl, Cardbot - Corner Connection.stl, Cardbot - Battery Tray.stl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]
2025-06-29 Added Laser Cut Files
2025-06-29 Create laser cut instructions
2025-07-07 Rename Cardbot - Corner Connection.stl to Cardbot - Corner Connector.stl
    [Cardbot - Corner Connector.stl]
2025-07-14 Added Part List
    [Cardbot Parts List.csv]
2025-07-14 Added Controller Files
    [Cardbot Controller-B_Cu.gbr, Cardbot Controller-B_Mask.gbr, Cardbot Controller-B_Paste.gbr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]
2025-07-14 Added Gerber and KiCad Files of PCB
    [Cardbot Controller-B_Cu.gbr, Cardbot Controller-B_Mask.gbr, Cardbot Controller-B_Paste.gbr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]
2025-07-14 Added Parts List
    [Controller Parts List.csv]
2025-07-14 Renamed whole file structure
    [Cardbot - Corner Bracket.stl, Cardbot - Corner Connector.stl, Cardbot - Battery Tray.stl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]
2025-07-15 Added v1.2 Files
    Updated:
    Updated STL to v1.2
    Updated Instructions
    Updated Parts List
    Added STEP files
    [Cardbot Body - Battery Tray.step, Cardbot Body - Battery Tray.stl, Cardbot Body - Corner Bracket.step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]
2025-07-31 Delete Cardbot Chassis/Cardbot - Tail.stl
    Removed Redundant Files
    [Cardbot - Tail.stl]
2025-07-31 Delete Cardbot Chassis/Cardbot - Corner Bracket.stl
    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
    [Cardbot - Corner Bracket.stl]
2025-07-31 Delete Cardbot Chassis/Cardbot - Corner Connector.stl
    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
    [Cardbot - Corner Connector.stl]
2025-07-31 Delete Cardbot Chassis/Cardbot - Battery Tray.stl
    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
    [Cardbot - Battery Tray.stl]
2025-07-31 Delete Cardbot Chassis/Cardbot - Motor Plate.stl
    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
    [Cardbot - Motor Plate.stl]
2025-07-31 Rename Cardbot - Body.svg to Cardbot Body - Frame.svg
    Renamed file to match new naming scheme.
2025-07-31 Update Laser Cut Instuctions.txt
    Added some further instructions.
2025-08-14 Clarified Header Text
    Clarified Header Text
    No longer mentions autonomous mode.
    [cardbot_robot_code-phone.ino]
2025-08-17 Improved part connections
    degreased the needed force to snap together following parts:
    Conner Bracker
    Battery Tray
    Tail
    [Cardbot Body - Battery Tray.step, Cardbot Body - Battery Tray.stl, Cardbot Body - Corner Bracket.step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]

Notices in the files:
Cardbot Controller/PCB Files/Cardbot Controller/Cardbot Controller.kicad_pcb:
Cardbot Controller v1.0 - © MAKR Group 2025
